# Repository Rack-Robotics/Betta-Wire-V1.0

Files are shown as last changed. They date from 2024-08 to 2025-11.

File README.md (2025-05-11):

# Betta-Wire-V1.0
Betta-Wire V1.0 is an affordable, open-source wire EDM machine designed for enthusiats. It allows users to cut electrically conductive materials such as steel and aluminum without the need for expensive industrial equipment like fiber lasers or CNC machines.

## Features 

- **Open Source**: Fully open-source design, allowing for community contributions and custom modifications.
- **User-3D-Printed**: Most components can be 3D printed, making it accessible and customizable.
- **Powercore Compatible**: Compatible with Powercore V2.0 EDM power supply.
- **4-Axis Motion**: Top and bottom EDM tools are capable of indepedent motion for X, Y, U, & V motion. 
- **Compact Build Area**: 100mm x 200mm, suitable for moderate-scale projects.
- **Hole Popping**: Cut starter holes for enclosed profiles using 1mm diameter hole popping electrodes.
- **Assisted Threading**: Easy controls for beginning threading and for detecting successful threading.
- **Material Compatibility**: Capable of cutting aluminum, steel, titanium, and other electrically conductive materials.

## Revisions 

### RevA

RevA is the prototype proof-of-concept version of the Betta-Wire V1.0. It served as the initial platform to test and validate the core functionality of the machine. While functional, it lacks some of the refinements and optimizations planned for the final kit version.

### RevB

RevB is the branch for the final version that will be used for the kit. This version includes all the improvements and optimizations based on the learnings from RevA. It is intended for distribution to users who will assemble the Betta-Wire V1.0 from the kit.

## Recommended Prerequisites

- 3D Printer (capable of printing carbon fiber PLA)
- Basic understanding of mechatronics and 3D printing
- Familiarity with Klipper firmware
 
 ## Legal & License

Shield: [][cc-by-nc]

This work is licensed under a
[Creative Commons Attribution-NonCommercial 4.0 International License][cc-by-nc].

[][cc-by-nc]

[cc-by-nc]: https://creativecommons.org/licenses/by-nc/4.0/
[cc-by-nc-image]: https://licensebuttons.net/l/by-nc/4.0/88x31.png
[cc-by-nc-shield]: https://img.shields.io/badge/License-CC%20BY--NC%204.0-lightgrey.svg

You are free to:
- Share — copy and redistribute the material in any medium or format
- Adapt — remix, transform, and build upon the material

Under the following terms:
- Attribution — You must give appropriate credit, provide a link to the license, and indicate if changes were made. You may do so in any reasonable manner, but not in any way that suggests the licensor endorses you or your use.
- NonCommercial — You may not use the material for commercial purposes.

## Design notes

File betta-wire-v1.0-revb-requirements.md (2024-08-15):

# Betta Wire V1.0, RevB Requirements
This document is for the recording of requirements for the Betta Wire V1.0, RevB. Requirements are organized by category, assembly, or component. All requirements must have a description and owner. Requirement headings are optimized for hyperlink referencing in other documents.  

## System Requirements
System-level requirements for the Betta Wire V1.0 RevB. This includes general constraints, such as system voltage or firmware.

| Requirement | Description | Owner | Importance | Rational |
| :---| :---| :---| :---| :---|
| Klipper Firmware | Use Klipper firmware | John (Rack Robotics)  | Mandatory | [Design Decision](Design-Decisions.md##Firmware)  |
| System Voltage | 24 VDC | John (Rack Robotics)  | Preferred | Industry Standard for FDM 3D printers | 
| EDM Wire Diameter | 0.3 mm | John (Rack Robotics)  | Preferred | [Design Decision](Design-Decisions.md##EDM-Wire)  | 

## Hardware Requirements
Requirements for hardware, such as fasteners. 
| Requirement | Description | Owner | Importance | Rational |
| :---| :---| :---| :---| :---|
| Fastener Material | Stainless Steel 316L (2) > Stainless Steel 304 | John (Rack Robotics)  | Mandatory | Resistance against corrosion in distilled water | 
| Fasteners Count | Minimize quantity & diversity of fasteners | John (Rack Robotics)  | Mandatory | Minimize cost and complexity | 
| Fastener Style | Metric, DIN 7991 Countersunk | John (Rack Robotics)  | Preferred | Flush mounting of fasteners in FDM prints |
| Fastener Type(s) | Pins > Countersunk M3 > Countersunk M4 > Countersunk M5 > Countersunk M6 | John (Rack Robotics)  | Mandatory | Minimize cost and complexity |

## 3D Printer Requirements
Requirements for 3D printing Betta Wire V1.0 components. The Betta Wire V1.0 is sold as a hardware kit, in the style of Voron. The plastic components are printed by the customer. This reduces kit cost significantly, and allows for user to customize their build's color scheme or materials.

> WARNING: CF-PA (carbon-fiber nylon) is not suitable for use on the Betta Wire or Wire Tool. CF-PA Filament deteriorates rapidly in water, loosing mechanical stiffness within days. Parts printed in CF-PA cannot be submerged in water. 

| Requirement | Description | Owner | Importance | Rational |
| :---| :---| :---| :---| :---|
| Minimum 3D Printer Build Area | X210 mm x Y210 mm x Z200 mm | John (Rack Robotics)  | Mandatory | Compatibility with common 3D printer build volumes|
| Recommended 3D Printer | Prusa MK4/MK3, Bambu X1C, Bambu P1P | John (Rack Robotics)  | Mandatory | Compatibility with common 3D printer build volumes|
| Recommended Filament | [CF-PLA](https://us.store.bambulab.com/products/pla-cf?variant=41003202248840) | John (Rack Robotics)  | Preferred | Excellent quality, minimum warping | 
| Alternative Filament | [ASA](https://www.prusa3d.com/category/prusament-asa/) | John (Rack Robotics)  | Preferred | Minimal warping compared to ABS |

## Hand Tool Requirements 
Requirements for hand tools for user assembly. 
| Requirement | Description | Owner |
| :---| :---| :---|
| Metric Allen Key Set | Allen key set for assembly of metric fasteners | John (Rack Robotics)  |
| Metric Drill Bits for Plastic | M5, M4, & M3 Drill bits for sizing holes in FDM 3D prints | John (Rack Robotics)  |
| Hand drill | Small handheld drill for drill bits | John (Rack Robotics)  |
| Gloves | Disposable gloves for applying super-glue and corrosion inhibitor | John (Rack Robotics)  |

## Controls Requirements 
Control requirements for the Betta Wire V1.0 RevB. Methods used to manage and direct the behavior of the machine and devices to achieve desired outputs. 

| Requirement | Description | Owner | Importance | Rational |
| :---| :---| :---| :---| :---|
| Open-Loop Motion Planning | Open-loop control of linear motion axis | John (Rack Robotics)  | Mandatory | [Design Decision](Design-Decisions.md###Why-not-closed-loop-motors-for-kinematics?) | 
| Open-Loop Wire Velocity | Open-loop control of EDM wire velocity | John (Rack Robotics)  | Preferred | Outside of project scope | 
| Closed-Loop Wire Tension | Maintain wire tension using closed-loop control | John (Rack Robotics)  | Mandatory | Improve machining reliability | 
| Closed-Loop Feedrate Control  | Adjust feedrate in response to EDM conditions | John (Rack Robotics)  | Mandatory | Improve machining reliability | 
| EDM PSU E-Shutdown | Automatically shutdown EDM PSU in the event of a prolonged short (PWM > short_threshold) | John (Rack Robotics)  | Mandatory | Safety, protection of PSU | 

## Kinematics
Kinematics requirements for the Betta Wire V1.0 RevB.

| Requirement | Description | Owner | Importance | Rational |
| :---| :---| :---| :---| :---|
| Dual CoreXY | Independently actuated dual coreXY systems | John (Rack Robotics)  | Mandatory | [Design Decision](Design-Decisions.md##RevB-Kinematics | 
| User Maintenance | Ensure means of replacing wear components in gantry | John (Rack Robotics)  | Mandatory | Improve user experience | 
| GT2 Timing Belts | Use GT2 timing belts with glass-core | John (Rack Robotics)  | Mandatory | Industry standard for FDM 3D printers | 
| Timing Belt Material | EPDM Rubber w/ glass-fiber fore | John (Rack Robotics)  | Mandatory | Reduce belt stretching over time | 

## Modules

### Overall Wire EDM Toolhead Requirements
The sender toolhead and receiver toolhead work together to control the position, tension, and velocity of the wire used for EDM cutting.

| Requirement | Description | Owner |
| :---| :---| :---|
| Maximum Tension of Wire | | John (Rack Robotics)  |
| Maximum Velocity of Wire | | John (Rack Robotics)  |
| Minimum Velocity of Wire | | John (Rack Robotics)  |
| Tube for Wire | Use 4 mm OD teflon tubing for wire interconnects | John (Rack Robotics)  |
| [IP68](#P68-Waterproofing) | Use IP68 rated motor for belt drive actuation | John (Rack Robotics)  |
| Testing | Design for testing on stationary test rig | John (Rack Robotics)  |

### Sender Toolhead Module Requirements
Requirements for the sender toolhead of the Betta Wire V1.0 RevB. The top toolhead sits above the water tank, on the bottom gantry. It is responsible for reporting EDM wire tension during machining, feeding new wire through the machine.

| Requirement | Description | Owner |
| :---| :---| :---|
| Belt Drive | Use belts to manipulate EDM wire | John (Rack Robotics)  |
| Tension Sensor | Use load cell for measuring wire tension | John (Rack Robotics)  |
| Energizer | Energize EDM wire with waveforms from Powercore EDM spark generator | John (Rack Robotics)  |
| Tube for Flushing | Use 4 mm OD PU tube for providing delivering 100 PSI water for flushing | John (Rack Robotics)  |

### Receiver Toolhead Module Requirements
Requirements for the receiver toolhead of the Betta Wire V1.0 RevB. The bottom toolhead sits inside the water tank, on the bottom gantry. It is responsible for receiving the EDM wire from the top toolhead, after passing through the cut. 

| Requirement | Description | Owner |
| :---| :---| :---|
| Belt Drive | Use belts to manipulate EDM wire | John (Rack Robotics)  |

### Waterproof Endstop Module
Requirements for waterproof endstops for homing kinematics

| Requirement | Description | Owner |
| :---| :---| :---|
| Hall Effect Sensor | Use a hall-effect sensor for detection of a 6 mm x 2 mm magnet on the toolhead/carriage | John (Rack Robotics)  |

### Wire Spool Box Module

### Waste Wire Box Module

### E-Box Module

## Custom Klipper Modifications

### Closed-Loop Feedrate Control
Requirements for closed-loop feedrate control using Klipper firmware: 

>Closed-loop control is a control-scheme that continuously monitors its output and automatically adjusts its inputs to maintain the desired output, using feedback to correct any deviations from the target performance. This ensures precision and stability in achieving the set goals.

Wire EDM failures often occur because the rate of travel (feedrate) of the electrode outpaces the material-removal rate (MRR). To eliminate this failure mode, the feedrate must be adjusted in response to feedback from the Powercore V2.0 spark generator. The Powercore V2.0 provides feedback using the PWM output port (ALRT). The PWM duty cycle is mapped to the Powercore's "observed spark ignition rate", which is strongly correlated to the material-removal rate. As the material-removal rate increases, the PWM duty cycle increases.

| PWM Duty Cycle | Description | Controls Response | 
| :---| :---| :---|
| 20% | No machining is occurring | Increase feedrate | 
| 80% | Optimum material-removal rate | Maintain feedrate | 
| 100% | Short circuit; EDM wire electrode has crashed into work | Decrease feedrate, or move backwards in program until short is clear  |

To achieve this behavior, new features must be added to Klipper: 

| Requirement | Description | Owner |
| :---| :---| :---|
| Read PWM Duty Cycle | Read PWM duty cycle of GPIO pin on control board, from PC-02 ALRT port | John (Rack Robotics)  |
| Automatic Feedrate Adjustment | Automatically increase/decrease/maintain feedrate in response to PWM duty cycle | John (Rack Robotics)  |
| Display feedback on GUI | Provide machine operator with PWM telemetry | John (Rack Robotics)  |
| Target Feedrate Range | 0.1 mm/min to 64 mm/min | John (Rack Robotics)  |
| Response Time | 100 ms to 1,000 ms | John (Rack Robotics)  |
| Feedrate Acceleration | Rate of change of feedrate must be limited | John (Rack Robotics)  | 
| Powercore V2.0 ALRT Port | 3.3 VDC | John (Rack Robotics)  |
| Powercore V2.0 PWM Frequency  | 10-100 KHz | John (Rack Robotics)  |

### Dual Gantry Motion Section for Klipper
Requirements for new Klipper kinematics module, allowing for independent control of two coreXY gantries. The secondary coreXY system is provides two additional axis: The U-axis and the V-axis. The U-axis is parallel to the X-axis, and the V-axis is parallel to the Y-axis.

| Requirement | Description | Owner |
| :---| :---| :---|
| Dual coreXY Motion Module | Allow for independent control over two coreXY gantries | John (Rack Robotics)  |
| Top coreXY Axis | X-axis & Y-axis | John (Rack Robotics)  | 
| Bottom coreUV Axis | U-axis & V-axis | John (Rack Robotics)  | 
| gcode example | G1 X69 Y420 U69 V420 | John (Rack Robotics)  |

### Wire EDM Toolhead Section for Klipper
Requirements for new Klipper section for use in printer.cfg, to be used for controlling wire tension. 

| Requirement | Description | Owner |
| :---| :---| :---|
| edm_wire_toolhead | Section name | John (Rack Robotics)  | 
| sensor_type | load cell | John (Rack Robotics)  | 
| sensor_range | 5 kg | John (Rack Robotics)  | 
| amplifier | HX711 | John (Rack Robotics)  | 
| control | PID | John (Rack Robotics)  | 
| edm_wire_sender | PWM pin for sender DC motor control | John (Rack Robotics)  | 
| edm_wire_receiver | PWM pin for receiver DC motor control | John (Rack Robotics)  | 
| mainsail telemetry | provide load cell value (newtons of force) to user in mainsail GUI (for front end engineer) | John (Rack Robotics)  | 

### Wire EDM Macros

**Macro for "wire_EDM_toolhead_diagnostic"**
Macro to test the maximum tension that the belt drive can provide. At the end of the test, the maximum value, in newtons of force, is printed for the user. 

- inform user 'conducting wire EDM toolhead diagnostic" 
- deactivate sender motor (PWM = 0)
- activate receiver motor (PWM = 255)
- measure load cell reading 
- print load cell value to user in newtons of force

**Macro for "wire_EDM_safe_pause"**
Macro for pausing the program during a wire cutting operation, without moving the tools. 

- inform user "pausing wire EDM"
- print current position of all axis to user
- deactivate EDM PSU to stop high-voltage (disable digital GPIO pin assigned to EDM PSU)
- stop motion 
- lock motors 
- do not home (to avoid crashing wire)

**Macro for "wire_EDM_toolhead_loading"**
Macro for loading wire into the belt drive systems. 

- print message to ask user to load EDM wire into sender
- turn on wire sender DC motor at specified PWM level 
- turn on wire receiver DC motor at specified PWM level 
- wait until the tension detected by the load cell increases, and then begin PID control loop, to make sure the wire is loaded
- stop DC motors 

**Macro for "wire_EDM_toolhead_unloading"**
Macro for unloading wire into the belt drive systems. 

- ask user to cut EDM wire 
- provide section for custom gcode commands
- stop DC motors

## IP68 Waterproofing

>An IP68 rating is an Ingress Protection (IP) code that indicates the degree of protection an electrical enclosure provides against the intrusion of solid objects (like dust) and liquids (like water). The IP code is defined by the International Electrotechnical Commission [(IEC) standard 60529](https://www.iec.ch/ip-ratings).

First Digit (6): Indicates the level of protection against solid particles.
- 6: Dust-tight. No ingress of dust; complete protection against contact (dustproof).

Second Digit (8): Indicates the level of protection against liquids.
- 8: Protection against continuous immersion in water. The equipment is suitable for continuous immersion in water under conditions specified by the manufacturer (usually means it can be submerged beyond 1 meter in depth, often up to 3 meters or more, for a specified period).

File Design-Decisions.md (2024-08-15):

# Betta Wire V1.0 RevB Design Decisions 

This page aims to illustrate the design decisions behind the Betta-Wire V1.0 revision B. This document pertains to RevB, the second revision of Betta Wire V1.0. RevB can be found in the RevB branch of the Betta Wire V1.0 repository. This page gives background information about the key design decisions of RevB only. 

## RevB Overview 
Betta Wire V1.0 RevB is a 4-axis wire EDM machine designed for enthusiasts. It is optimized to provide a low barrier of entry for persons interested in wire EDM for prototyping, and manufacturing robotics.

**Improvements over RevA**
- Improved user experience
- Improved precision
- Improved accuracy
- Reduced setup time 
- Closed-loop wire tension control 
- Closed-loop feedrate control

## RevB Toolheads
The toolheads are subassemblies of the Betta Wire which control the EDM wire. The top toolhead is located on the top gantry. The bottom toolhead is located on the bottom gantry. The toolheads are responsible for controlling wire location, tension, and velocity. 

Design Goals for RevB Wire EDM Toolheads 
- Measure wire tension and report value to control board
- Control wire tension via DC motor
- Control wire velocity via DC motor
- Minimize required volume to improve build space
- Support re-threading of EDM wire without removal of the Betta Wire from the aquarium tank 

The RevB toolheads are inspired by the [Papilio](https://kevinakasam.com/papilio/), a 3D printer extruder optimized for pushing 1.75 mm filament. 

## RevB Kinematics 
The kinematics of the Betta Wire were designed to maximize performance while maintaining a reasonable construction cost.

**Why not linear rails?** Linear rails able to operate underwater are not readily available. To use linear rails, while maintaining a reasonable cost, requires a sub $35 dollar solution.

**Dual Core-XY**: The Betta Wire V1.0 RevB is a dual core-xy machine. Each toolhead is independently controlled by one core-xy system: The four core-xy motors (A, B, C, D) allow for movement in four axis (X, Y, U, V). The top gantry (A & B) moves the top tool, while the bottom gantry (C & D) moves the bottom tool. This permits cutting angles walls, tappers, and chamfers. 

**Remote Power Transmission**: Mechanical power is transmitted from the C & D motors to the bottom gantry by a stainless steel axel. This axel rotates GT2 timing belt pulleys, which actuate the core-xy kinematics remotely. This scheme eliminates the need for water-proof motors, by moving the NEMA 17s above the waterline. Reducing the cost of components here permits resources to be invested into other portions of the Betta Wire, such as the tools and controls.

### Why not closed-loop motors for kinematics? 
Closed-loop motors present a significant control systems challenge for Klipper firmware. Integration of closed-loop motor controls for A, B, C & D motors would require a complete redesign of Klipper’s architecture.

### What is closed-loop feedrate control? 
Closed-loop feedrate control is the adjustment of the rate of machine travel, in response to feedback from the EDM power supply / spark-generator. When the feedrate is too slow, the machine automatically increases speed to optimize the material removal rate. This ensures that the Betta Wire is always cutting at the maximum safe speed.

## General Improvements
General improvements over RevA: 

- Endstops for automatic homing
- Suction-cup mounting of e-box, and other accessory modules for easier assembly and maintenance

## Motherboard & Electronics
- The Manta M5P was chosen for it’s compact integration of a 32-bit microcontroller, up to five motor drivers, and a single-board computer. The dual coreXXY kinematics require 4 motor drivers, leaving 1 motor driver available for future expansions.   

## Firmware 
The Betta Wire V1.0 uses [Klipper](https://www.klipper3d.org) firmware. Klipper permits rapid revisions without the need for recompiling. In addition to a host of features: Wireless connectivity, a GUI, compatibility with most 3D printer control hardware, support for advances sensors, USB, CAN, UART, I2C, and an active development community.

## EDM Power / Spark-Generator 
The Betta Wire V1.0 utilizes the Powercore V1.0 wire EDM power supply. This is an open-source EDM power supply designed and sold by Rack Robotics, Inc.

## EDM Wire
0.3 mm Diameter hardened brass wire was selected as a compromise between maximizing tensile strength, maximizing current capacity, and minimizing cut diameter.

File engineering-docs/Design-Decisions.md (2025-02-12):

# Betta Wire V1.0 RevB Design Decisions 
This page aims to illustrate the design decisions behind the Betta-Wire V1.0 revision B. This page gives background information about the key design decisions of RevB only. 

## RevB Overview 
Betta Wire V1.0 RevB is a 4-axis wire EDM machine designed for enthusiasts. It is optimized to provide a low barrier of entry for persons interested in wire EDM for prototyping, and manufacturing.

**Improvements over RevA**
- Improved user experience
- Improved precision
- Improved accuracy
- Reduced setup time 
- Closed-loop wire tension control 
- Closed-loop feedrate control

## RevB Toolheads
The toolheads are subassemblies of the Betta Wire which control the EDM wire. The top toolhead is located on the top gantry. The bottom toolhead is located on the bottom gantry. The toolheads are responsible for controlling wire location, tension, and velocity. 

Design Goals for RevB Wire EDM Toolheads 
- Measure wire tension and report value to control board
- Control wire tension via DC motor
- Control wire velocity via DC motor
- Minimize required volume to improve build space
- Support semi-automiatic re-threading of EDM wire

The RevB toolheads are inspired by the [Papilio](https://kevinakasam.com/papilio/), a 3D printer extruder optimized for pushing 1.75 mm filament. 

## RevB Kinematics
The kinematics of the Betta Wire were designed to maximize performance while maintaining a reasonable construction cost.

### Why not linear rails?
Linear rails able to operate underwater are not readily available. To use linear rails, while maintaining a reasonable cost, requires a sub $35 dollar solution.

### Dual Core-XY
The Betta Wire V1.0 RevB is a dual core-xy machine. Each toolhead is independently controlled by one core-xy system: The four core-xy motors (A, B, C, D) allow for movement in four axis (X, Y, U, V). The top gantry (A & B) moves the top tool, while the bottom gantry (C & D) moves the bottom tool. This permits cutting angled walls, tappers, and chamfers.

### Remote Power Transmission
Mechanical power is transmitted from the C & D motors to the bottom gantry by a stainless steel axel. This axel rotates GT2 timing belt pulleys, which actuate the core-xy kinematics remotely. This scheme eliminates the need for water-proof motors, by moving the NEMA 17s above the waterline. Reducing the cost of components here permits resources to be invested into other portions of the Betta Wire, such as the tools and controls.

### What is closed-loop feedrate control? 
Closed-loop feedrate control is the adjustment of the rate of machine travel, in response to feedback from the EDM power supply / spark-generator. When the feedrate is too slow, the machine automatically increases speed to optimize the material removal rate. This ensures that the Betta Wire is always cutting at the maximum safe speed.

## General Improvements
General improvements over RevA: 
- Endstops for automatic homing
- Improved kinematics to prevent binding and racking
- Stainless steel components to prevent corrosion

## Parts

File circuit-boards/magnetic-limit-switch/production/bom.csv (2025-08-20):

Designator | Footprint | Quantity | Value | LCSC Part #
C1 | 0603 | 1 | 1 uF | C106248
U1 | SOT-23-3 | 1 | TMAG5231 | C17378950

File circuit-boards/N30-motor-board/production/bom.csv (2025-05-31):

Designator | Footprint | Quantity | Value | LCSC Part #
C1, C2 | 0603 | 2 | 0.1 uF | C113803
J1 | SolderWire-0.25sqmm_1x01_D0.65mm_OD1.7mm | 1 | MOTOR+
J2 | SolderWire-0.25sqmm_1x01_D0.65mm_OD1.7mm | 1 | MOTOR-
M1, M2 | N30_MOTOR_TH | 2 | BDC_N30_MOTOR_01
R1 | 0603 | 1 | 10K | C98220
TP2, TP3, TP4, TP5 | TestPoint_Pad_2.0x2.0mm | 4 | TestPoint

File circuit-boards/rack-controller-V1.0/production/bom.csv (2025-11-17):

Designator | Footprint | Quantity | Value | LCSC Part #
C10, C65, C66, C67, C68, C8, C83, C84 | 0603 | 8 | 0.1uF | C113803
C100, C14, C15, C16, C17, C18, C19, C20, C21, C22, C23, C60, C62, C69, C70, C79, C80, C85, C86, C95, C96, C97, C98, C99 | CP_Elec_6.3x5.9 | 24 | 47u | C264034
C11, C12, C13, C34, C35, C36, C37, C38 | 0603 | 8 | 100nF | C113803
C24, C25, C26, C27, C28, C29, C30, C31, C32, C33, C59, C61, C63, C64, C71, C72, C73, C74, C81, C82, C87, C88, C89, C9, C90, C91, C92, C93, C94 | 1206 | 29 | 10 uF | C96600
C3, C4, C5, C6 | 0603 | 4 | 2.2uF | C106853
C39, C40, C41, C42, C43, C44, C45, C46, C47, C48, C49, C50, C51, C52, C53, C54, C55, C56, C57, C58, C75, C76, C77, C78 | 0402 | 24 | 100pF | C576700
D1, D2, D3, D4, D5 | D_SMC | 5 | SMCJ60A | C2943780
D10, D11, D12, D13, D14, D15, D16, D17, D18, D19, D20, D21, D22, D23, D24, D25, D30, D31, D6, D7, D8, D9 | D_SMA | 22 | SMAJ51CA | C135003
D26, D27, D32 | D_SOD-128 | 3 | PMEG10030ELPX | C5260346
D33 | D_SMA | 1 | US1M-13-F | C99333
HDR1_2, HDR1, HDR2_2, HDR2, HDR3, HDR4, HDR5, HDR6, HDR7, HDR8 | PinSocket_1x08_P2.54mm_Vertical | 10 | PinSocket_1x08_P2.54mm_Vertical | C27438
J1, J17, J18, J19, J9 | 2601-1102 | 5 | 2601-1102
J10, J11, J12, J13, J14, J6 | JST_XH_S4B-XH-SM4-TB_1x04-1MP_P2.50mm_Horizontal_custom | 6 | S4B-XH-SM4-TB | C161861
J15, J16, J2, J3, J4, J5, J7 | S3B-XH-SM4-TB | 7 | S3B-XH-SM4-TB | C161860
J20 | PinHeader_1x03_P2.54mm_Vertical | 1 | BDC_00_SELECTOR | C5360899
J21 | PinHeader_1x03_P2.54mm_Vertical | 1 | BDC_01_SELECTOR | C5360899
J8 | raspberrypi | 1 | Raspberry Pi GPIO Header | NULL
L10, L11, L12, L13, L14, L15, L16, L17, L18, L19, L20, L21, L22, L23, L24, L27, L28, L29, L30, L31, L5, L6, L7, L8, L9 | 0402 | 25 | BBUP00100505330Y00 | C668299
L25, L26, L32 | SRR1210-8R2Y | 3 | 8.2 uH
R1, R100, R104, R18, R19, R2, R22, R23, R26, R27, R30, R31, R34, R35, R5, R6, R7, R8, R9, R96, R98 | 0603 | 21 | 1K | C22548
R10, R11, R12, R13, R14, R16, R20, R24, R28, R3, R32, R36, R37, R38, R39, R4, R40, R41, R43, R45, R47, R49, R51, R52, R53, R54, R55, R56, R92, R93, R94 | 0603 | 31 | 10K | C98220
R101, R102, R103 | 0603 | 3 | 19.6K | C245925
R57, R58, R59, R60, R61, R62, R63, R64, R65, R66, R67, R68, R69, R70, R71, R72, R73, R74, R75, R76, R85, R86, R87, R88 | 0603 | 24 | 150R | C114608
R77, R78, R89 | 0603 | 3 | 49.9K
R79, R81, R90 | 0603 | 3 | 100K | C728638
R80, R82 | 0603 | 2 | 9.09K | C185301
R83, R84 | 2512 | 2 | 0.11R | C46595965
R91 | 0603 | 1 | 17.8K | C185364
R95, R97, R99 | 0603 | 3 | 2.2K | C114662
RP4 | raspberrypi-outline | 1 | Raspberry_Pi
U1, U2, U3, U4, U5 | BTT_TMC2209_V1.3 | 5 | TMC2209_SILENTSTEPSTICK | NULL
U10, U6, U7 | LV14360PDDAR | 3 | LV14360PDDAR | C2864599
U11, U12, U13 | TPS1HTC30-Q1 | 3 | TPS1HTC30AQPWPRQ1 | C22414694
U8, U9 | DRV8870DDA | 2 | DRV8870DDA | C86590

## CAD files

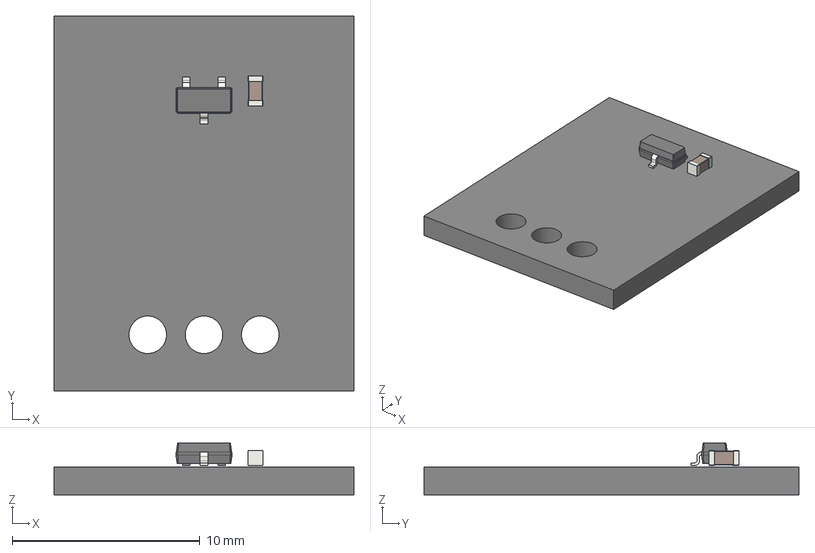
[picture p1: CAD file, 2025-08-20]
circuit-boards/magnetic-limit-switch/3D-models/magnetic-limit-switch-D.step
16.0 x 20.0 x 2.76 mm
SOT-23-3
C_0603_1608Metric
magnetic-limit-switch_PCB

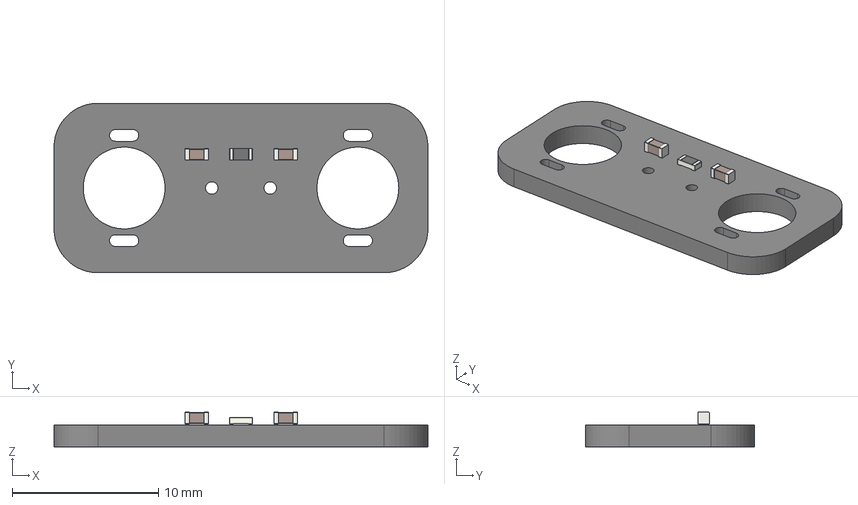
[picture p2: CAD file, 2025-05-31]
circuit-boards/N30-motor-board/production/N30-motor-board-RevA.step
25.6 x 11.6 x 2.37 mm
C_0603_1608Metric x 2
R_0603_1608Metric
N30-motor-board_PCB

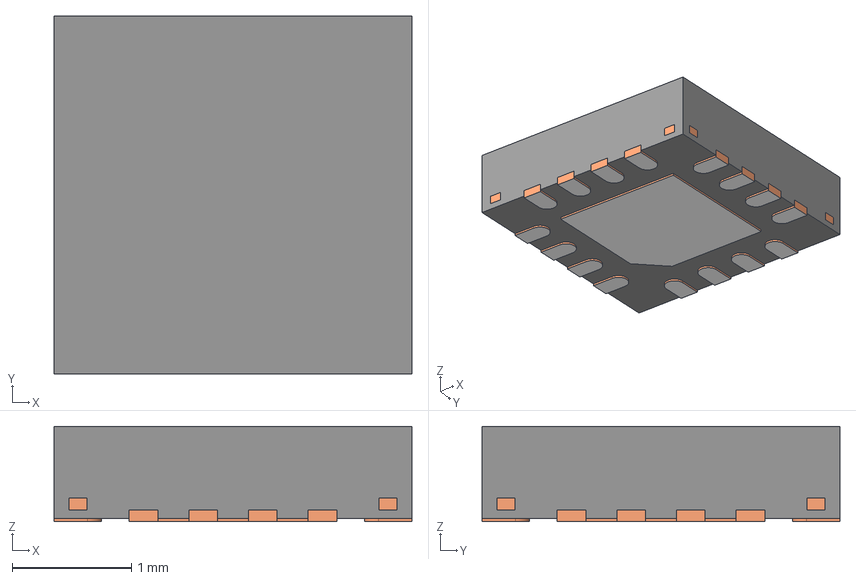
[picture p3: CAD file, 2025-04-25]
circuit-boards/rack-controller-V1.0/3D-models/DRV8235RTER.stp
3.00 x 3.00 x 0.8 mm
BODY-QFN
FRAME-RTE0016C
PIN1-ID

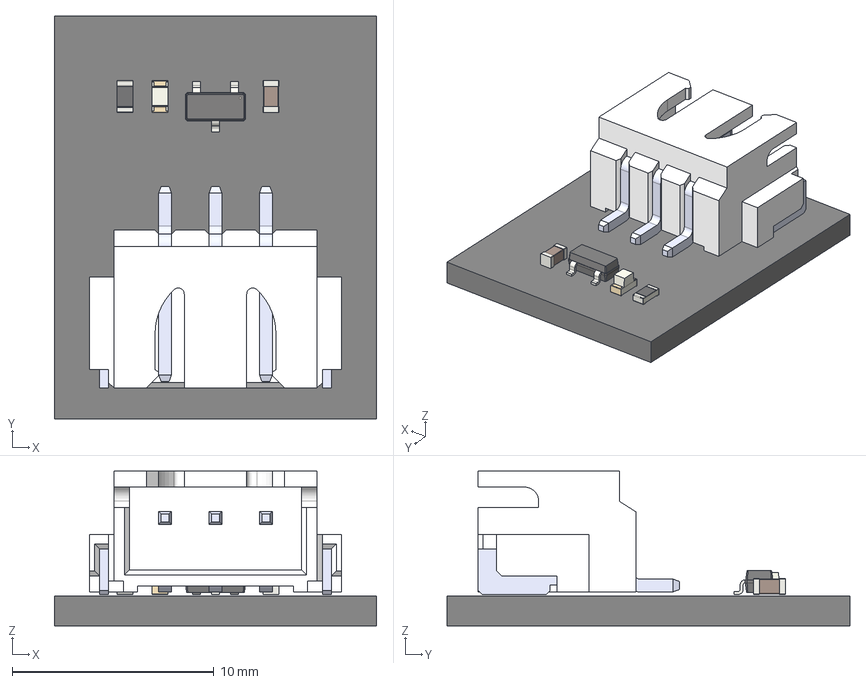
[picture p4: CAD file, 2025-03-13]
circuit-boards/magnetic-limit-switch/3D-models/magnetic-limit-switch-C.step
16.0 x 20.0 x 7.69 mm
SOT-23-3
SxB-XH-SM4-TB_3
pin^SxB-XH-SM4-TB Ass x 3
R_0603_1608Metric
C_0603_1608Metric
LED_0603_1608Metric
magnetic-limit-switch_PCB

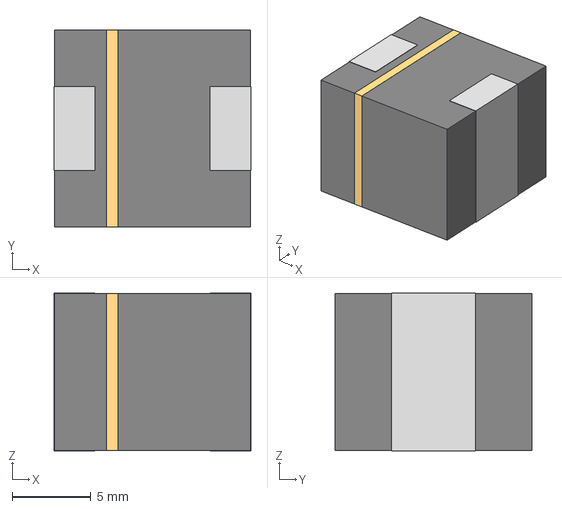
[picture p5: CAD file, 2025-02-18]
circuit-boards/rack-controller-V1.0/3D-models/SRR1210-8R2Y.step
12.5 x 12.5 x 10.0 mm

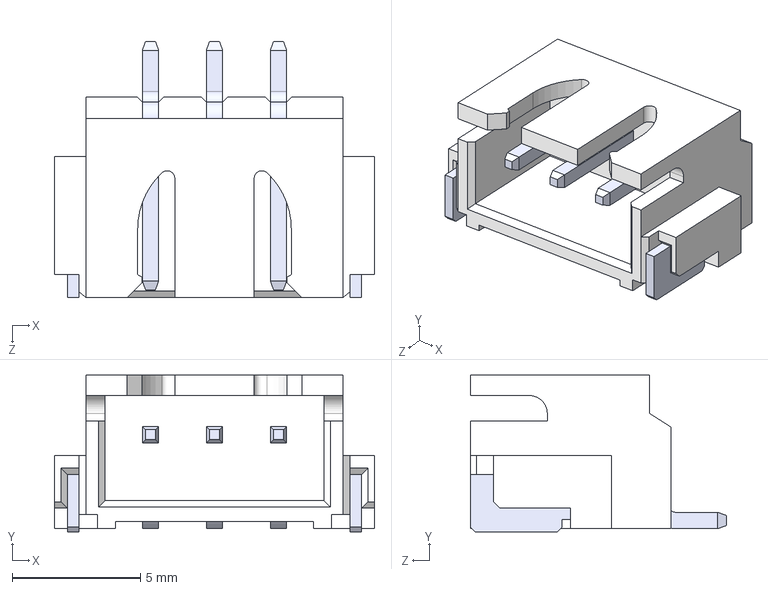
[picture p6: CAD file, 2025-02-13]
circuit-boards/magnetic-limit-switch/3D-models/S3B-XH-SM4-TB.STEP
12.5 x 6.12 x 10.0 mm
SxB-XH-SM4-TB_3
pin^SxB-XH-SM4-TB Ass x 3

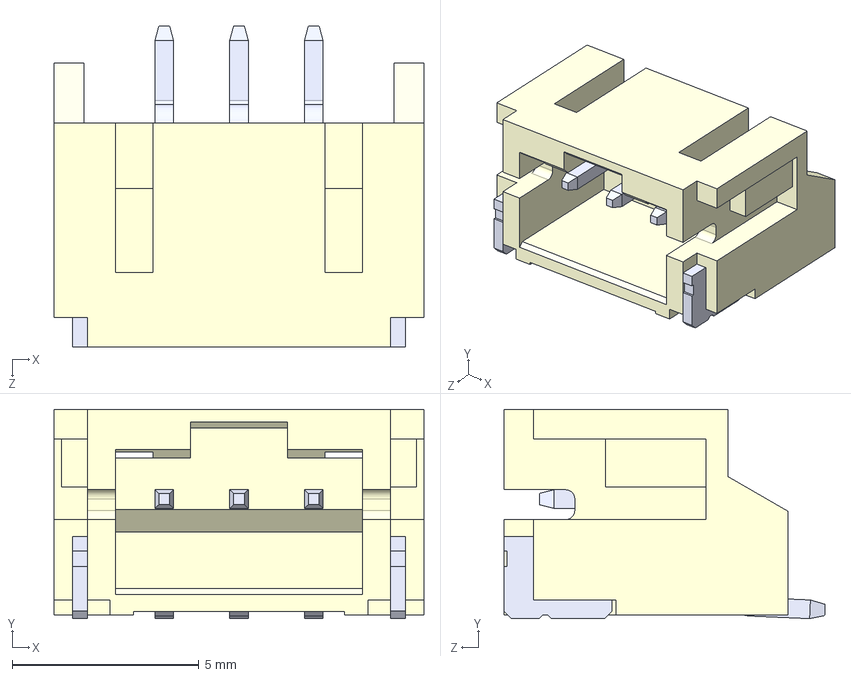
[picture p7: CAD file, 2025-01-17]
circuit-boards/magnetic-limit-switch/3D-models/S3B-PH-SM4-TB.step
9.90 x 5.60 x 8.60 mm

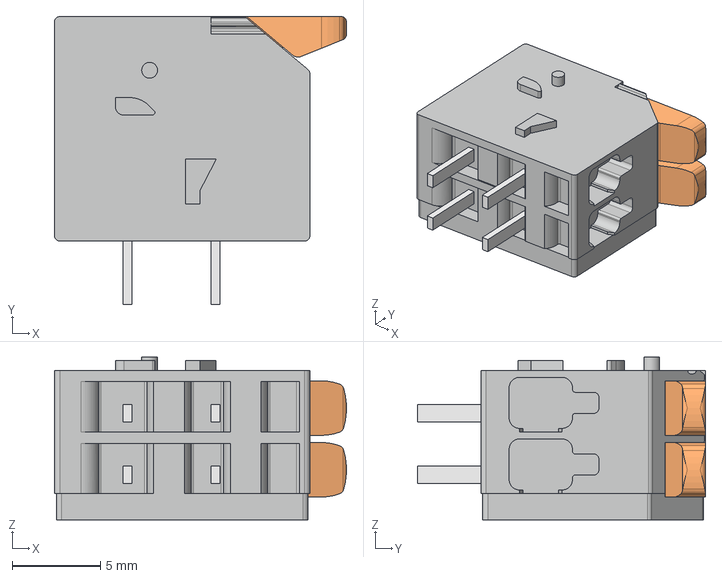
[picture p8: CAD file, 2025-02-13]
circuit-boards/rack-controller-V1.0/3D-models/2601-1102.stp
16.6 x 16.4 x 9.25 mm

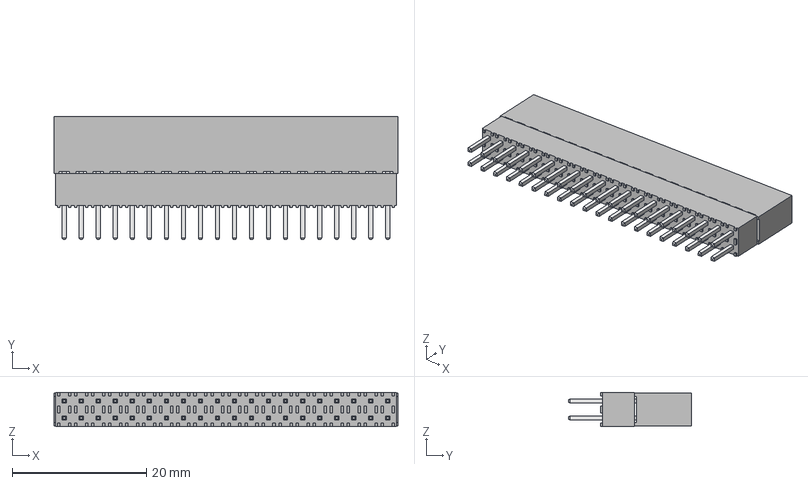
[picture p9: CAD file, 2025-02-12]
circuit-boards/rack-controller-V1.0/3D-models/ESQ-120-23-T-D.step
51.3 x 18.4 x 5.08 mm
ESQ-120-23-T-D_socket
ESQ-120-23-T-D_pins
ESQ-120-23-T-D2_pins
ESQ-120-23-G-D-LL_bpins

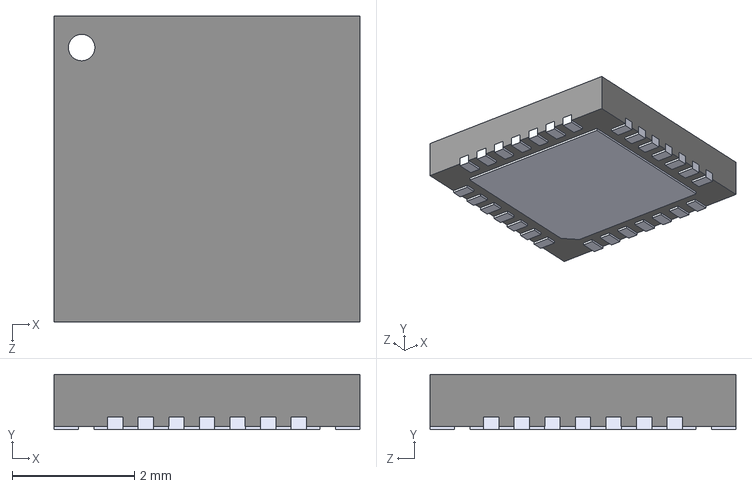
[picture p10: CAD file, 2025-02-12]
circuit-boards/rack-controller-V1.0/3D-models/TMC2209-LA.step
5.00 x 0.9 x 5.00 mm

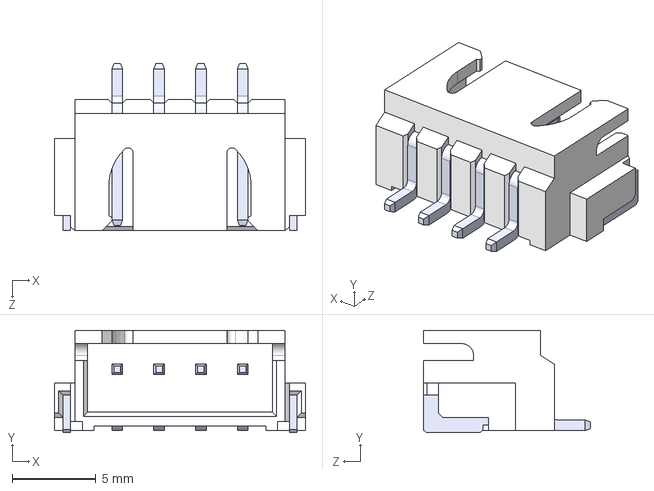
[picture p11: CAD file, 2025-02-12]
circuit-boards/rack-controller-V1.0/3D-models/S4B-XH-SM4-TB.STEP
15.0 x 6.12 x 10.0 mm
SxB-XH-SM4-TB_4
pin^SxB-XH-SM4-TB Ass x 4

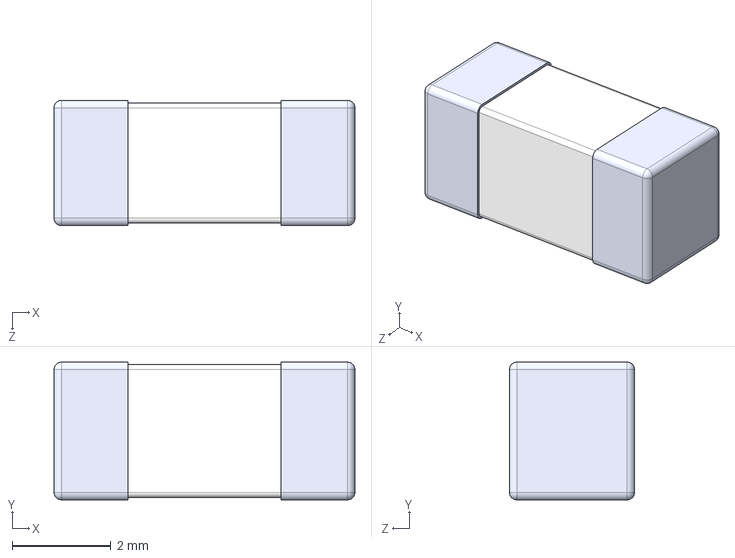
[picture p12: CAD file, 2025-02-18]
circuit-boards/rack-controller-V1.0/3D-models/0679H9120-05.step
6.10 x 2.79 x 2.54 mm

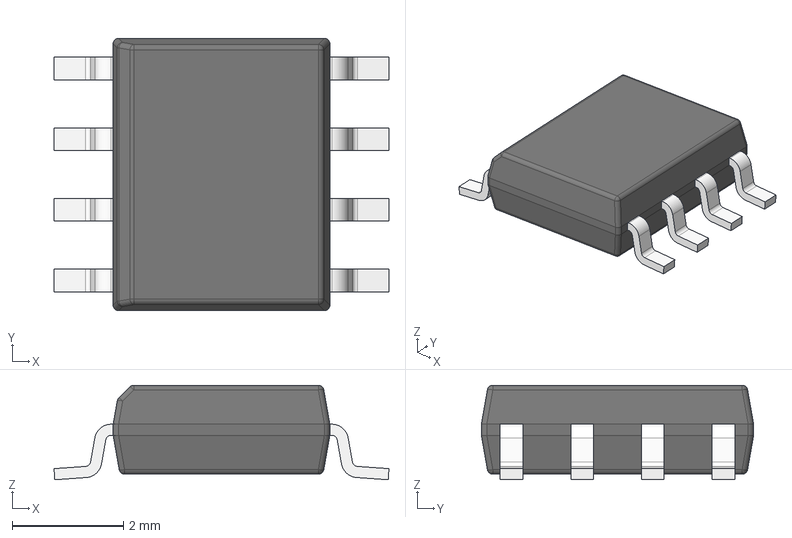
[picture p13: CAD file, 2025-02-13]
circuit-boards/rack-controller-V1.0/3D-models/LMR36520ADDAR.stp
6.03 x 4.90 x 1.70 mm
BODY-SO
LEAD-SO x 8
THERMALPAD-SO

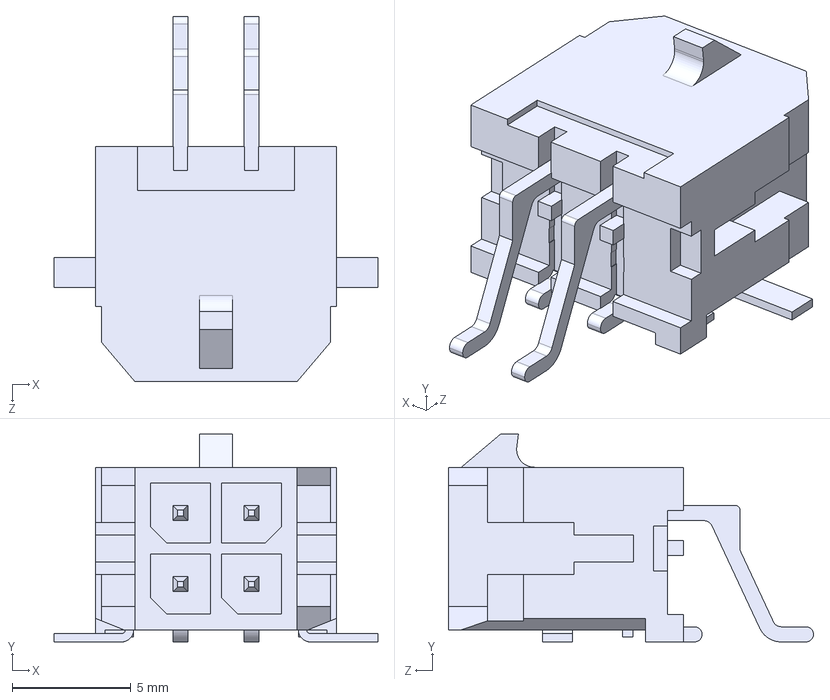
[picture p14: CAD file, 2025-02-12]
circuit-boards/rack-controller-V1.0/3D-models/430450409.step
13.7 x 8.77 x 15.4 mm
043045xxxx_04
tab^043045xxxx ass
pin^043045xxxx ass x 2

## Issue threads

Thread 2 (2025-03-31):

add to features

mkinney, 2025-03-31:
Reading back on the discord, it looks like these features are going to be present:
- assisted threading
- hole popping

Might want to add that to the features

Cooper-RackRobo, 2025-05-05:
Good idea. Added.

Closed 2025-05-05.

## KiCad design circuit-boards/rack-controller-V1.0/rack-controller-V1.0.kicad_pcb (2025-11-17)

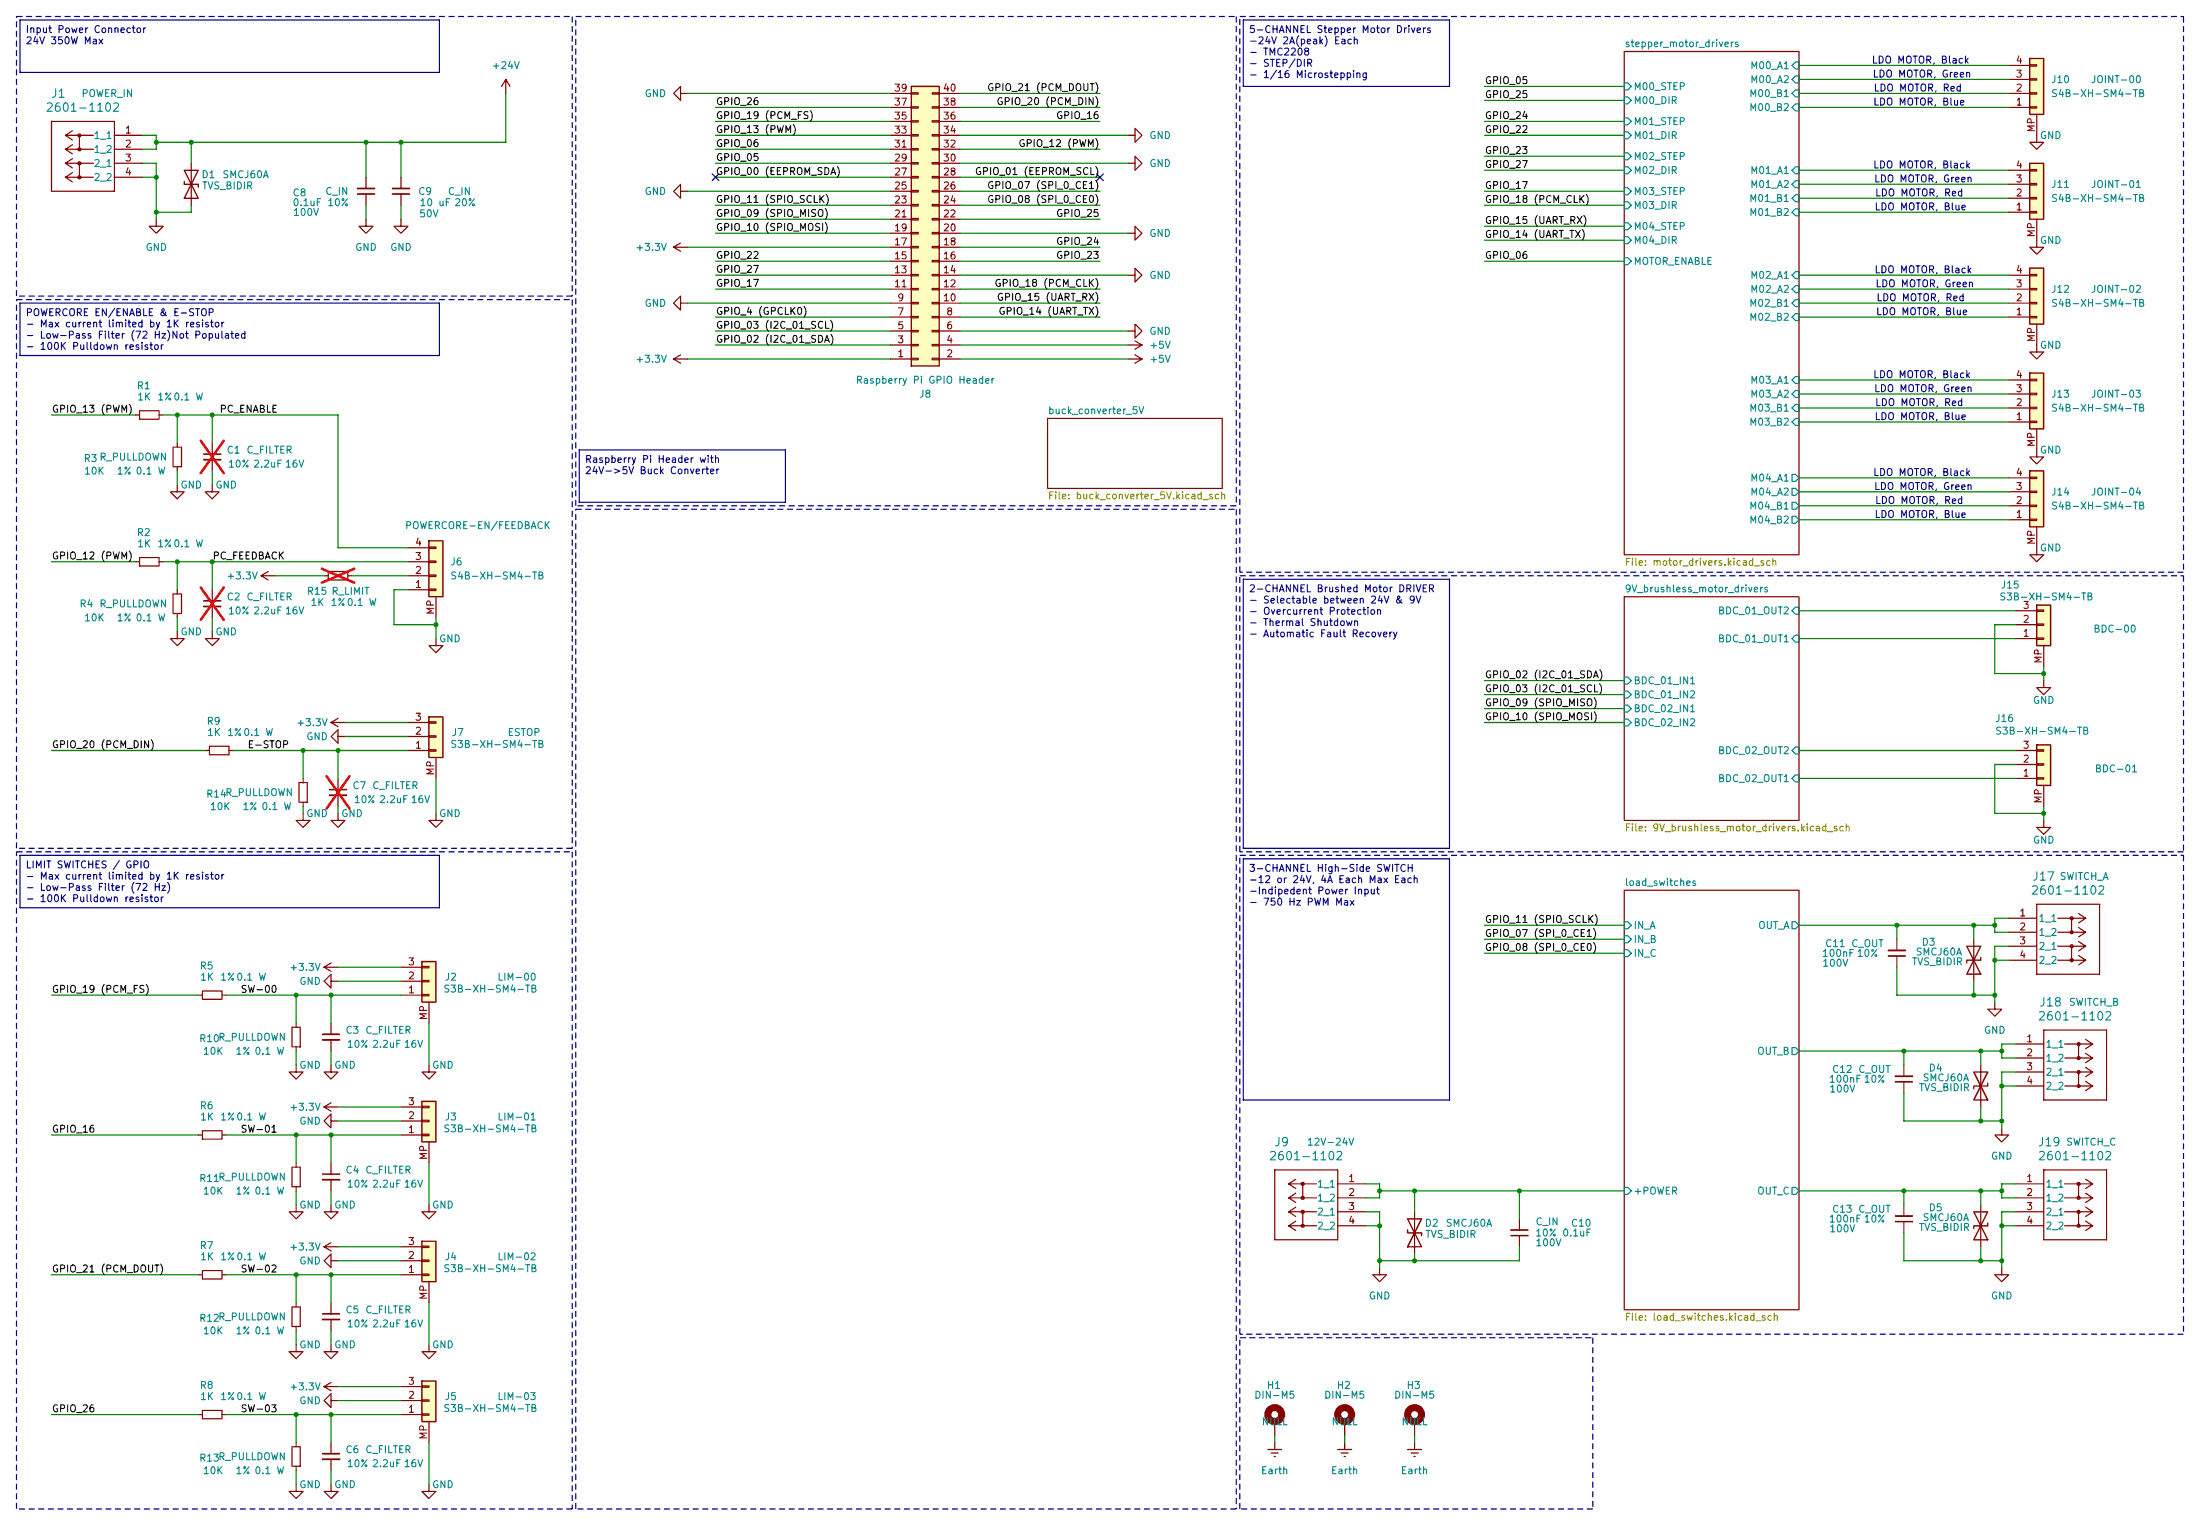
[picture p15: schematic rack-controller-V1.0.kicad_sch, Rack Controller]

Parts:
C1, C2, C7: 2.2uF; C_0603_1608Metric; Max Voltage 16V; Tolerance 10%; Manufacturer# CC0603KRX5R7BB225; LCSC Part # C106853; not fitted
C3, C4, C5, C6: 2.2uF; C_0603_1608Metric; Max Voltage 16V; Tolerance 10%; Manufacturer# CC0603KRX5R7BB225; LCSC Part # C106853
C8, C10: 0.1uF; C_0603_1608Metric; Tolerance 10%; Max Voltage 100V; Manufacturer# CC0603KRX7R0BB104; LCSC Part # C113803
C9: 10 uF; C_1206_3216Metric; Tolerance 20%; Max Voltage 50V; Manufacturer# CL31A106MBHNNNE; LCSC Part # C96600
C11, C12, C13: 100nF; C_0603_1608Metric; Voltage 100V; Tolerance 10%; Manufacturer# CC0603KRX7R0BB104; LCSC Part # C113803
D1, D2, D3, D4, D5: SMCJ60A; D_SMC; Manufacturer# SMCJ60CA-13-F; LCSC Part # C2943780
H1, H2, H3: DIN-M5; MountingHole_5.3mm_M5_DIN965_Pad_TopBottom; Manufacturer# NULL; LCSC Part # NULL
J1, J9, J17, J18, J19: 2601-1102; Manufacturer# 2601-1102
J2, J3, J4, J5, J7, J15, J16: S3B-XH-SM4-TB; Manufacturer# JST Sales America Inc.; LCSC Part # C161860
J6, J10, J11, J12, J13, J14: S4B-XH-SM4-TB; JST_XH_S4B-XH-SM4-TB_1x04-1MP_P2.50mm_Horizontal_custom; Manufacturer# S4B-XH-SM4-TB; LCSC Part # C161861
J8: Raspberry Pi GPIO Header; raspberrypi; Manufacturer# ESQ-120-23-T-D; LCSC Part # NULL
R1, R2, R5, R6, R7, R8, R9: 1K; R_0603_1608Metric; Tolerance 1%; Manufacturer# RC0603FR-071KL; LCSC Part # C22548
R3, R4, R10, R11, R12, R13, R14: 10K; R_0603_1608Metric; Tolerance 1%; Manufacturer# RC0603BR-0710KL; LCSC Part # C98220
R15: 1K; R_0603_1608Metric; Tolerance 1%; Manufacturer# RC0603FR-071KL; LCSC Part # C22548; not fitted

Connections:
+3.3V: J2.3, J3.3, J4.3, J5.3, J7.3, J8.1, J8.17, R15.1; also elsewhere on the board
+5V: J8.2, J8.4; also elsewhere on the board
+24V: C8.2, C9.2, D1.2 (A2), J1.1 (1_1), J1.2 (1_2); also elsewhere on the board
/9V_brushless_motor_drivers/BDC_01_OUT1: J15.1; also elsewhere on the board
/9V_brushless_motor_drivers/BDC_01_OUT2: J15.3; also elsewhere on the board
/9V_brushless_motor_drivers/BDC_02_OUT1: J16.1; also elsewhere on the board
/9V_brushless_motor_drivers/BDC_02_OUT2: J16.3; also elsewhere on the board
/E-STOP: C7.1, J7.1, R9.2, R14.2
/GPIO_00 (EEPROM_SDA): J8.27
/GPIO_01 (EEPROM_SCL): J8.28
/GPIO_02 (I2C_01_SDA): J8.3; also elsewhere on the board
/GPIO_03 (I2C_01_SCL): J8.5; also elsewhere on the board
/GPIO_4 (GPCLK0): J8.7
/GPIO_05: J8.29; also elsewhere on the board
/GPIO_06: J8.31; also elsewhere on the board
/GPIO_07 (SPI_0_CE1): J8.26; also elsewhere on the board
/GPIO_08 (SPI_0_CE0): J8.24; also elsewhere on the board
/GPIO_09 (SPIO_MISO): J8.21; also elsewhere on the board
/GPIO_10 (SPIO_MOSI): J8.19; also elsewhere on the board
/GPIO_11 (SPIO_SCLK): J8.23; also elsewhere on the board
/GPIO_12 (PWM): J8.32, R2.1
/GPIO_13 (PWM): J8.33, R1.1
/GPIO_14 (UART_TX): J8.8; also elsewhere on the board
/GPIO_15 (UART_RX): J8.10; also elsewhere on the board
/GPIO_16: J8.36, R6.1
/GPIO_17: J8.11; also elsewhere on the board
/GPIO_18 (PCM_CLK): J8.12; also elsewhere on the board
/GPIO_19 (PCM_FS): J8.35, R5.1
/GPIO_20 (PCM_DIN): J8.38, R9.1
/GPIO_21 (PCM_DOUT): J8.40, R7.1
/GPIO_22: J8.15; also elsewhere on the board
/GPIO_23: J8.16; also elsewhere on the board
/GPIO_24: J8.18; also elsewhere on the board
/GPIO_25: J8.22; also elsewhere on the board
/GPIO_26: J8.37, R8.1
/GPIO_27: J8.13; also elsewhere on the board
/PC_ENABLE: C1.1, J6.4, R1.2, R3.2
/PC_FEEDBACK: C2.1, J6.3, R2.2, R4.2
/SW-00: C3.1, J2.1, R5.2, R10.2
/SW-01: C4.1, J3.1, R6.2, R11.2
/SW-02: C5.1, J4.1, R7.2, R12.2
/SW-03: C6.1, J5.1, R8.2, R13.2
/load_switches/+POWER: C10.2, D2.2 (A2), J9.1 (1_1), J9.2 (1_2); also elsewhere on the board
/load_switches/OUT_A: C11.2, D3.2 (A2), J17.1 (1_1), J17.2 (1_2); also elsewhere on the board
/load_switches/OUT_B: C12.2, D4.2 (A2), J18.1 (1_1), J18.2 (1_2); also elsewhere on the board
/load_switches/OUT_C: C13.2, D5.2 (A2), J19.1 (1_1), J19.2 (1_2); also elsewhere on the board
/stepper_motor_drivers/M00_A1: J10.4; also elsewhere on the board
/stepper_motor_drivers/M00_A2: J10.3; also elsewhere on the board
/stepper_motor_drivers/M00_B1: J10.2; also elsewhere on the board
/stepper_motor_drivers/M00_B2: J10.1; also elsewhere on the board
/stepper_motor_drivers/M01_A1: J11.4; also elsewhere on the board
/stepper_motor_drivers/M01_A2: J11.3; also elsewhere on the board
/stepper_motor_drivers/M01_B1: J11.2; also elsewhere on the board
/stepper_motor_drivers/M01_B2: J11.1; also elsewhere on the board
/stepper_motor_drivers/M02_A1: J12.4; also elsewhere on the board
/stepper_motor_drivers/M02_A2: J12.3; also elsewhere on the board
/stepper_motor_drivers/M02_B1: J12.2; also elsewhere on the board
/stepper_motor_drivers/M02_B2: J12.1; also elsewhere on the board
/stepper_motor_drivers/M03_A1: J13.4; also elsewhere on the board
/stepper_motor_drivers/M03_A2: J13.3; also elsewhere on the board
/stepper_motor_drivers/M03_B1: J13.2; also elsewhere on the board
/stepper_motor_drivers/M03_B2: J13.1; also elsewhere on the board
/stepper_motor_drivers/M04_A1: J14.4; also elsewhere on the board
/stepper_motor_drivers/M04_A2: J14.3; also elsewhere on the board
/stepper_motor_drivers/M04_B1: J14.2; also elsewhere on the board
/stepper_motor_drivers/M04_B2: J14.1; also elsewhere on the board
Earth: H1.1, H2.1, H3.1
GND: C1.2, C2.2, C3.2, C4.2, C5.2, C6.2, C7.2, C8.1, C9.1, C10.1, C11.1, C12.1, C13.1, D1.1 (A1), D2.1 (A1), D3.1 (A1), D4.1 (A1), D5.1 (A1), J1.3 (2_1), J1.4 (2_2), J2.2, J2.MP, J3.2, J3.MP, J4.2, J4.MP, J5.2, J5.MP, J6.1, J6.MP, J7.2, J7.MP, J8.6, J8.9, J8.14, J8.20, J8.25, J8.30, J8.34, J8.39, J9.3 (2_1), J9.4 (2_2), J10.MP, J11.MP, J12.MP, J13.MP, J14.MP, J15.2, J15.MP, J16.2, J16.MP, J17.3 (2_1), J17.4 (2_2), J18.3 (2_1), J18.4 (2_2), J19.3 (2_1), J19.4 (2_2), R3.1, R4.1, R10.1, R11.1, R12.1, R13.1, R14.1; also elsewhere on the board
unnamed: J6.2, R15.2

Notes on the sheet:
LDO MOTOR, Green
LDO MOTOR, Blue
LDO MOTOR, Black
LDO MOTOR, Red
2-CHANNEL Brushed Motor DRIVER - Selectable between 24V & 9V - Overcurrent Protection - Thermal Shutdown - Automatic Fault Recovery
LIMIT SWITCHES / GPIO - Max current limited by 1K resistor - Low-Pass Filter (72 Hz) - 100K Pulldown resistor
5-CHANNEL Stepper Motor Drivers -24V 2A(peak) Each - TMC2208 - STEP/DIR - 1/16 Microstepping
POWERCORE EN/ENABLE & E-STOP - Max current limited by 1K resistor - Low-Pass Filter (72 Hz)Not Populated - 100K Pulldown resistor
3-CHANNEL High-Side SWITCH -12 or 24V, 4A Each Max Each -Indipedent Power Input - 750 Hz PWM Max
Input Power Connector 24V 350W Max
Raspberry Pi Header with 24V->5V Buck Converter

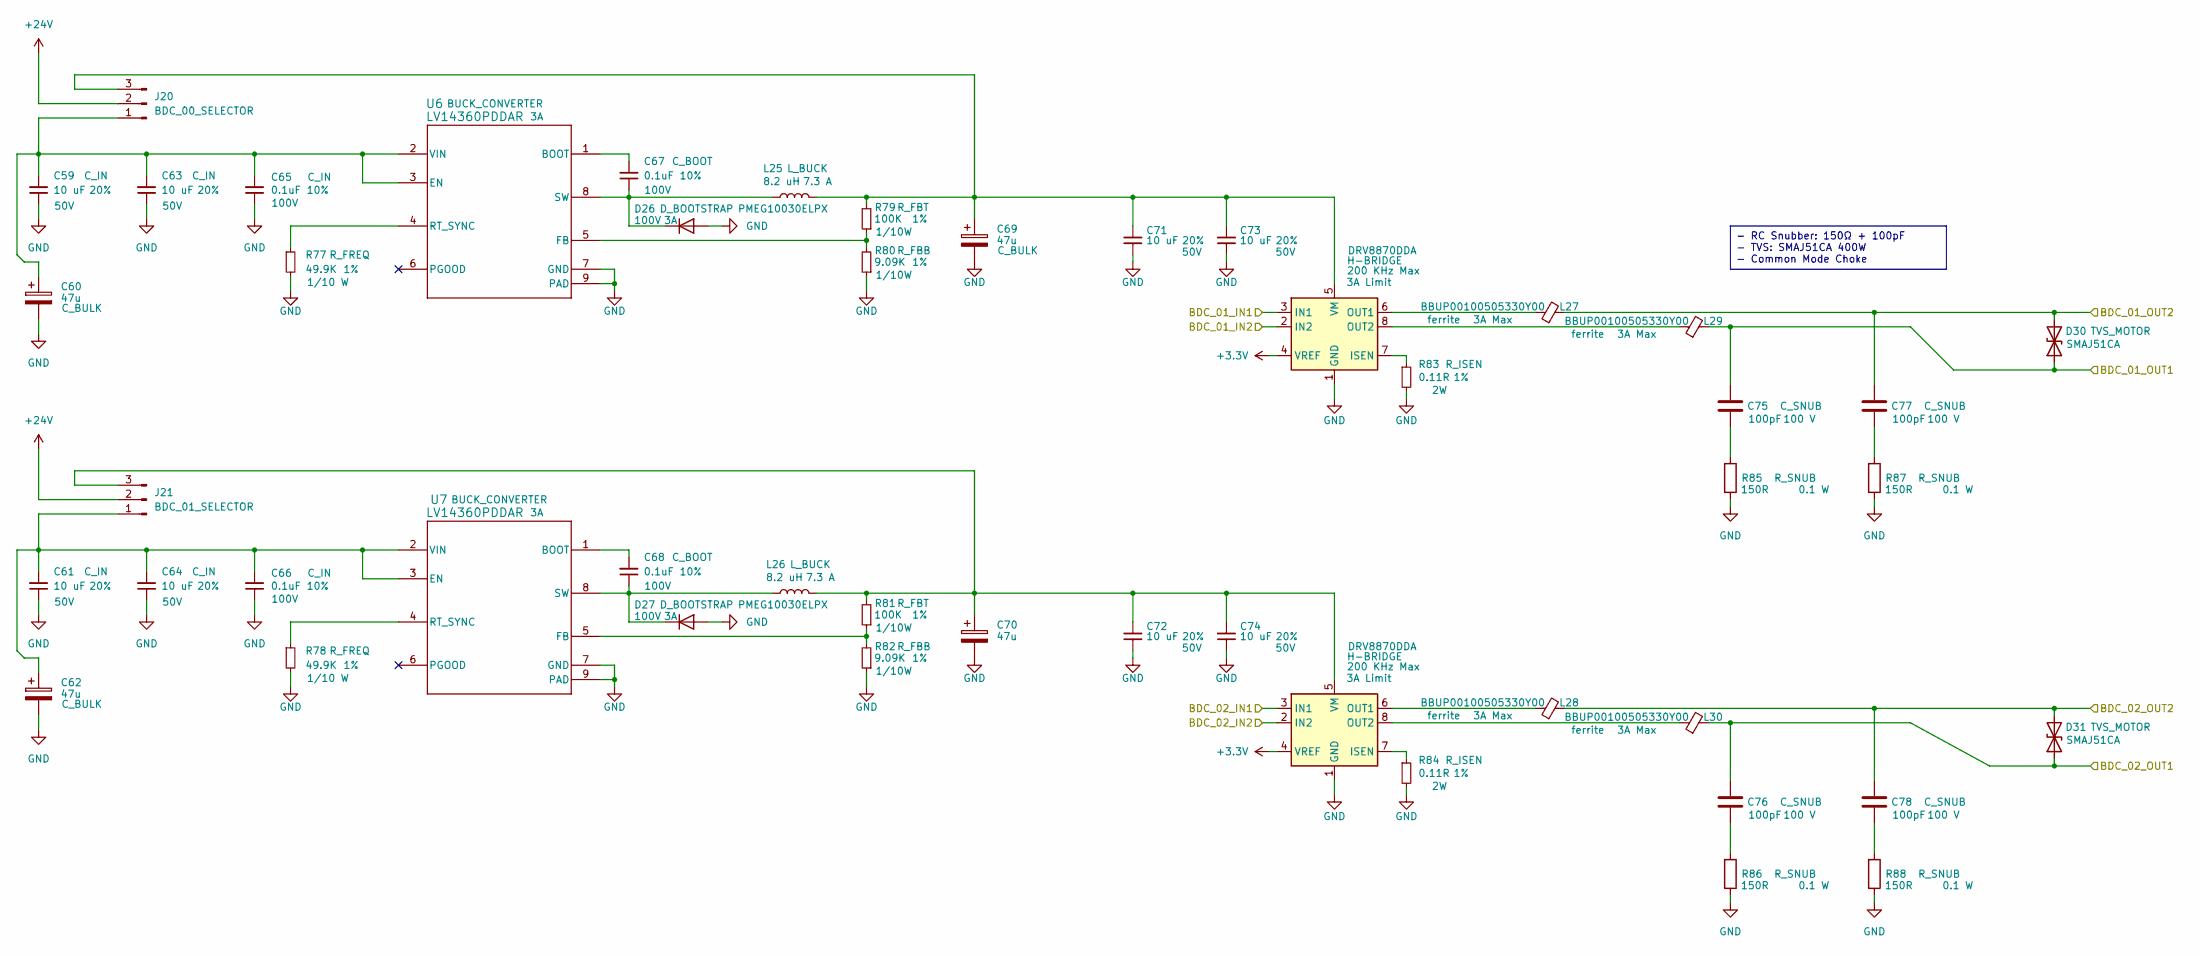
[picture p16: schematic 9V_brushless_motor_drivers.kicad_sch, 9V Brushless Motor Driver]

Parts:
C59, C61, C63, C64, C71, C72, C73, C74: 10 uF; C_1206_3216Metric; Tolerance 20%; Max Voltage 50V; Manufacturer# CL31A106MBHNNNE; LCSC Part # C96600
C60, C62, C69, C70: 47u; CP_Elec_6.3x5.9; Manufacturer# 35SVPK47M; LCSC Part # C264034
C65, C66, C67, C68: 0.1uF; C_0603_1608Metric; Tolerance 10%; Max Voltage 100V; Manufacturer# CC0603KRX7R0BB104; LCSC Part # C113803
C75, C76, C77, C78: 100pF; C_0402_1005Metric; Voltage 100 V; Manufacturer# CC0402JRNPO0BN101; LCSC Part # C576700
D26, D27: PMEG10030ELPX; D_SOD-128; Max Voltage 100V; Manufacturer# PMEG10030ELPX; LCSC Part # C5260346
D30, D31: SMAJ51CA; D_SMA; Manufacturer# SMAJ60CA-13-F; LCSC Part # C135003
J20: BDC_00_SELECTOR; PinHeader_1x03_P2.54mm_Vertical; Manufacturer# PZ2.54-1*3; LCSC Part # C5360899
J21: BDC_01_SELECTOR; PinHeader_1x03_P2.54mm_Vertical; Manufacturer# PZ2.54-1*3; LCSC Part # C5360899
L25, L26: 8.2 uH; SRR1210-8R2Y; Manufacturer# SRR1210-8R2Y
L27, L28, L29, L30: BBUP00100505330Y00; L_0402_1005Metric; Manufacturer# BLM15AX100SN1D; LCSC Part # C668299
R77, R78: 49.9K; R_0603_1608Metric; Tolerance 1%; Manufacturer# RC0603FR-0749K9L
R79, R81: 100K; R_0603_1608Metric; Tolerance 1%; Manufacturer# RT0603FRE07100KL; LCSC Part # C728638
R80, R82: 9.09K; R_0603_1608Metric; Tolerance 1%; Manufacturer# RC0603FR-079K09L; LCSC Part # C185301
R83, R84: 0.11R; R_2512_6332Metric; Tolerance 1%; Manufacturer# YHR2512SE2WR110F4; LCSC Part # C46595965
R85, R86, R87, R88: 150R; R_0603_1608Metric; Tolerance 1%; Manufacturer# RC0603FR-07150RL; LCSC Part # C114608
U6, U7: LV14360PDDAR; Manufacturer# LV14360PDDAR; LCSC Part # C2864599
U8, U9: DRV8870DDA; Manufacturer# DRV8870DDAR; LCSC Part # C86590

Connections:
+3.3V: U8.4 (VREF), U9.4 (VREF); also elsewhere on the board
+24V: J20.2, J21.2; also elsewhere on the board
/9V_brushless_motor_drivers/BDC_01_OUT1: C75.1, D30.1 (A1), L29.2; also elsewhere on the board
/9V_brushless_motor_drivers/BDC_01_OUT2: C77.1, D30.2 (A2), L27.2; also elsewhere on the board
/9V_brushless_motor_drivers/BDC_02_OUT1: C76.1, D31.1 (A1), L30.2; also elsewhere on the board
/9V_brushless_motor_drivers/BDC_02_OUT2: C78.1, D31.2 (A2), L28.2; also elsewhere on the board
/GPIO_02 (I2C_01_SDA): U8.3 (IN1); also elsewhere on the board
/GPIO_03 (I2C_01_SCL): U8.2 (IN2); also elsewhere on the board
/GPIO_09 (SPIO_MISO): U9.3 (IN1); also elsewhere on the board
/GPIO_10 (SPIO_MOSI): U9.2 (IN2); also elsewhere on the board
GND: C59.1, C60.2, C61.1, C62.2, C63.1, C64.1, C65.1, C66.1, C69.2, C70.2, C71.1, C72.1, C73.1, C74.1, D26.2 (A), D27.2 (A), R77.2, R78.2, R80.1, R82.1, R83.2, R84.2, R85.2, R86.2, R87.2, R88.2, U6.7 (GND), U6.9 (PAD), U7.7 (GND), U7.9 (PAD), U8.1 (GND), U8.9 (GND), U9.1 (GND), U9.9 (GND); also elsewhere on the board
unnamed: C75.2, R85.1
unnamed: C76.2, R86.1
unnamed: C77.2, R87.1
unnamed: C78.2, R88.1
unnamed: C67.1, D26.1 (K), L25.1, U6.8 (SW)
unnamed: C68.1, D27.1 (K), L26.1, U7.8 (SW)
unnamed: C59.2, C60.1, C63.2, C65.2, J20.1, U6.2 (VIN), U6.3 (EN)
unnamed: C69.1, C71.2, C73.2, J20.3, L25.2, R79.2, U8.5 (VM)
unnamed: C61.2, C62.1, C64.2, C66.2, J21.1, U7.2 (VIN), U7.3 (EN)
unnamed: C70.1, C72.2, C74.2, J21.3, L26.2, R81.2, U9.5 (VM)
unnamed: C67.2, U6.1 (BOOT)
unnamed: R79.1, R80.2, U6.5 (FB)
unnamed: R77.1, U6.4 (RT_SYNC)
unnamed: C68.2, U7.1 (BOOT)
unnamed: R81.1, R82.2, U7.5 (FB)
unnamed: R78.1, U7.4 (RT_SYNC)
unnamed: R83.1, U8.7 (ISEN)
unnamed: L27.1, U8.6 (OUT1)
unnamed: L29.1, U8.8 (OUT2)
unnamed: R84.1, U9.7 (ISEN)
unnamed: L28.1, U9.6 (OUT1)
unnamed: L30.1, U9.8 (OUT2)

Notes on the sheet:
- RC Snubber: 150Ω + 100pF - TVS: SMAJ51CA 400W - Common Mode Choke

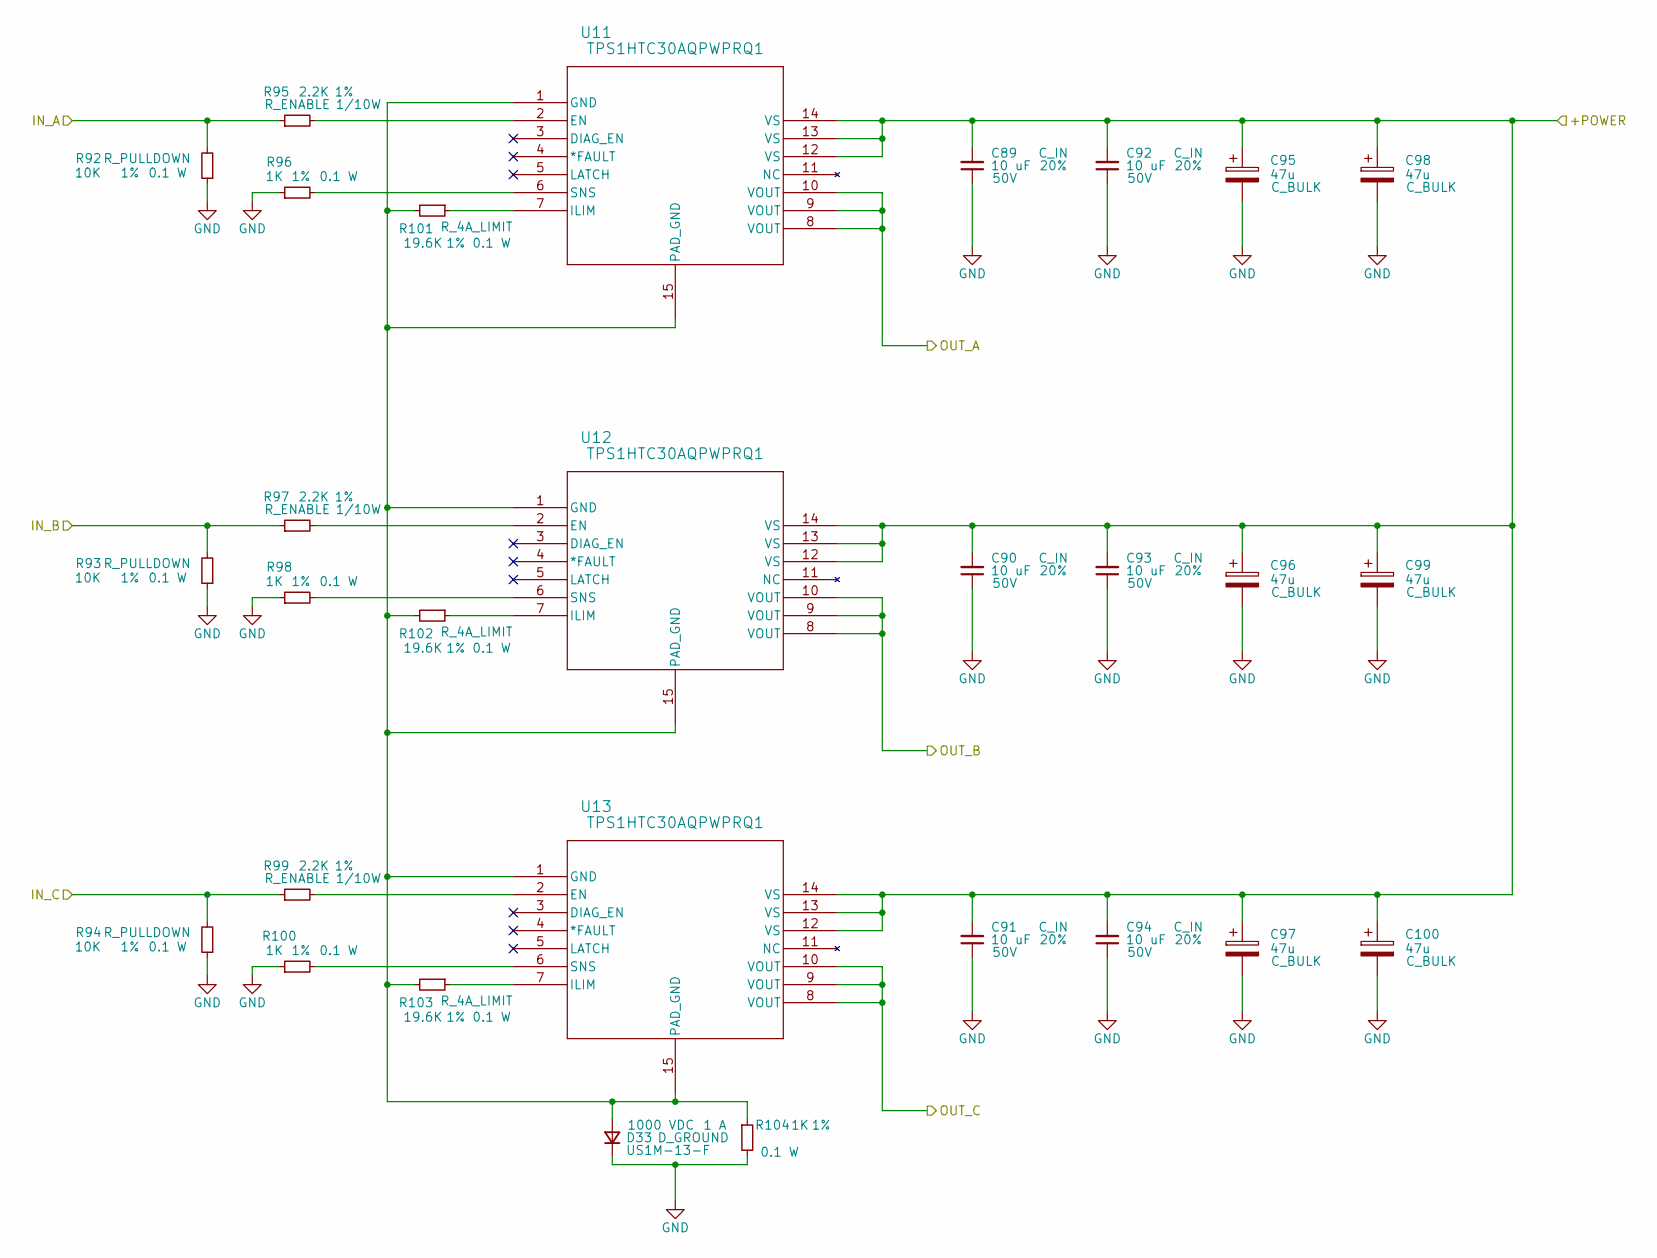
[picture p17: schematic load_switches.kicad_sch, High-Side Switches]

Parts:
C89, C90, C91, C92, C93, C94: 10 uF; C_1206_3216Metric; Tolerance 20%; Max Voltage 50V; Manufacturer# CL31A106MBHNNNE; LCSC Part # C96600
C95, C96, C97, C98, C99, C100: 47u; CP_Elec_6.3x5.9; Manufacturer# 35SVPK47M; LCSC Part # C264034
D33: US1M-13-F; D_SMA; Tolerance NULL; Manufacturer# US1M-13-F; LCSC Part # C99333
R92, R93, R94: 10K; R_0603_1608Metric; Tolerance 1%; Manufacturer# RC0603BR-0710KL; LCSC Part # C98220
R95, R97, R99: 2.2K; R_0603_1608Metric; Tolerance 1%; Manufacturer# RC0603FR-072K2L; LCSC Part # C114662
R96, R98, R100, R104: 1K; R_0603_1608Metric; Tolerance 1%; Manufacturer# RC0603FR-071KL; LCSC Part # C22548
R101, R102, R103: 19.6K; R_0603_1608Metric; Tolerance 1%; Manufacturer# RC0603FR-0719K6L; LCSC Part # C245925
U11, U12, U13: TPS1HTC30AQPWPRQ1; TPS1HTC30-Q1; Manufacturer# TPS1HTC30AQPWPRQ1; LCSC Part # C22414694

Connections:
/GPIO_07 (SPI_0_CE1): R93.2, R97.1; also elsewhere on the board
/GPIO_08 (SPI_0_CE0): R94.2, R99.1; also elsewhere on the board
/GPIO_11 (SPIO_SCLK): R92.2, R95.1; also elsewhere on the board
/load_switches/+POWER: C89.2, C90.2, C91.2, C92.2, C93.2, C94.2, C95.1, C96.1, C97.1, C98.1, C99.1, C100.1, U11.12 (VS), U11.13 (VS), U11.14 (VS), U12.12 (VS), U12.13 (VS), U12.14 (VS), U13.12 (VS), U13.13 (VS), U13.14 (VS); also elsewhere on the board
/load_switches/OUT_A: U11.8 (VOUT), U11.9 (VOUT), U11.10 (VOUT); also elsewhere on the board
/load_switches/OUT_B: U12.8 (VOUT), U12.9 (VOUT), U12.10 (VOUT); also elsewhere on the board
/load_switches/OUT_C: U13.8 (VOUT), U13.9 (VOUT), U13.10 (VOUT); also elsewhere on the board
GND: C89.1, C90.1, C91.1, C92.1, C93.1, C94.1, C95.2, C96.2, C97.2, C98.2, C99.2, C100.2, D33.1 (K), R92.1, R93.1, R94.1, R96.1, R98.1, R100.1, R104.2; also elsewhere on the board
unnamed: D33.2 (A), R101.2, R102.2, R103.2, R104.1, U11.1 (GND), U11.15 (PAD_GND), U12.1 (GND), U12.15 (PAD_GND), U13.1 (GND), U13.15 (PAD_GND)
unnamed: R95.2, U11.2 (EN)
unnamed: R101.1, U11.7 (ILIM)
unnamed: R96.2, U11.6 (SNS)
unnamed: R97.2, U12.2 (EN)
unnamed: R102.1, U12.7 (ILIM)
unnamed: R98.2, U12.6 (SNS)
unnamed: R99.2, U13.2 (EN)
unnamed: R103.1, U13.7 (ILIM)
unnamed: R100.2, U13.6 (SNS)

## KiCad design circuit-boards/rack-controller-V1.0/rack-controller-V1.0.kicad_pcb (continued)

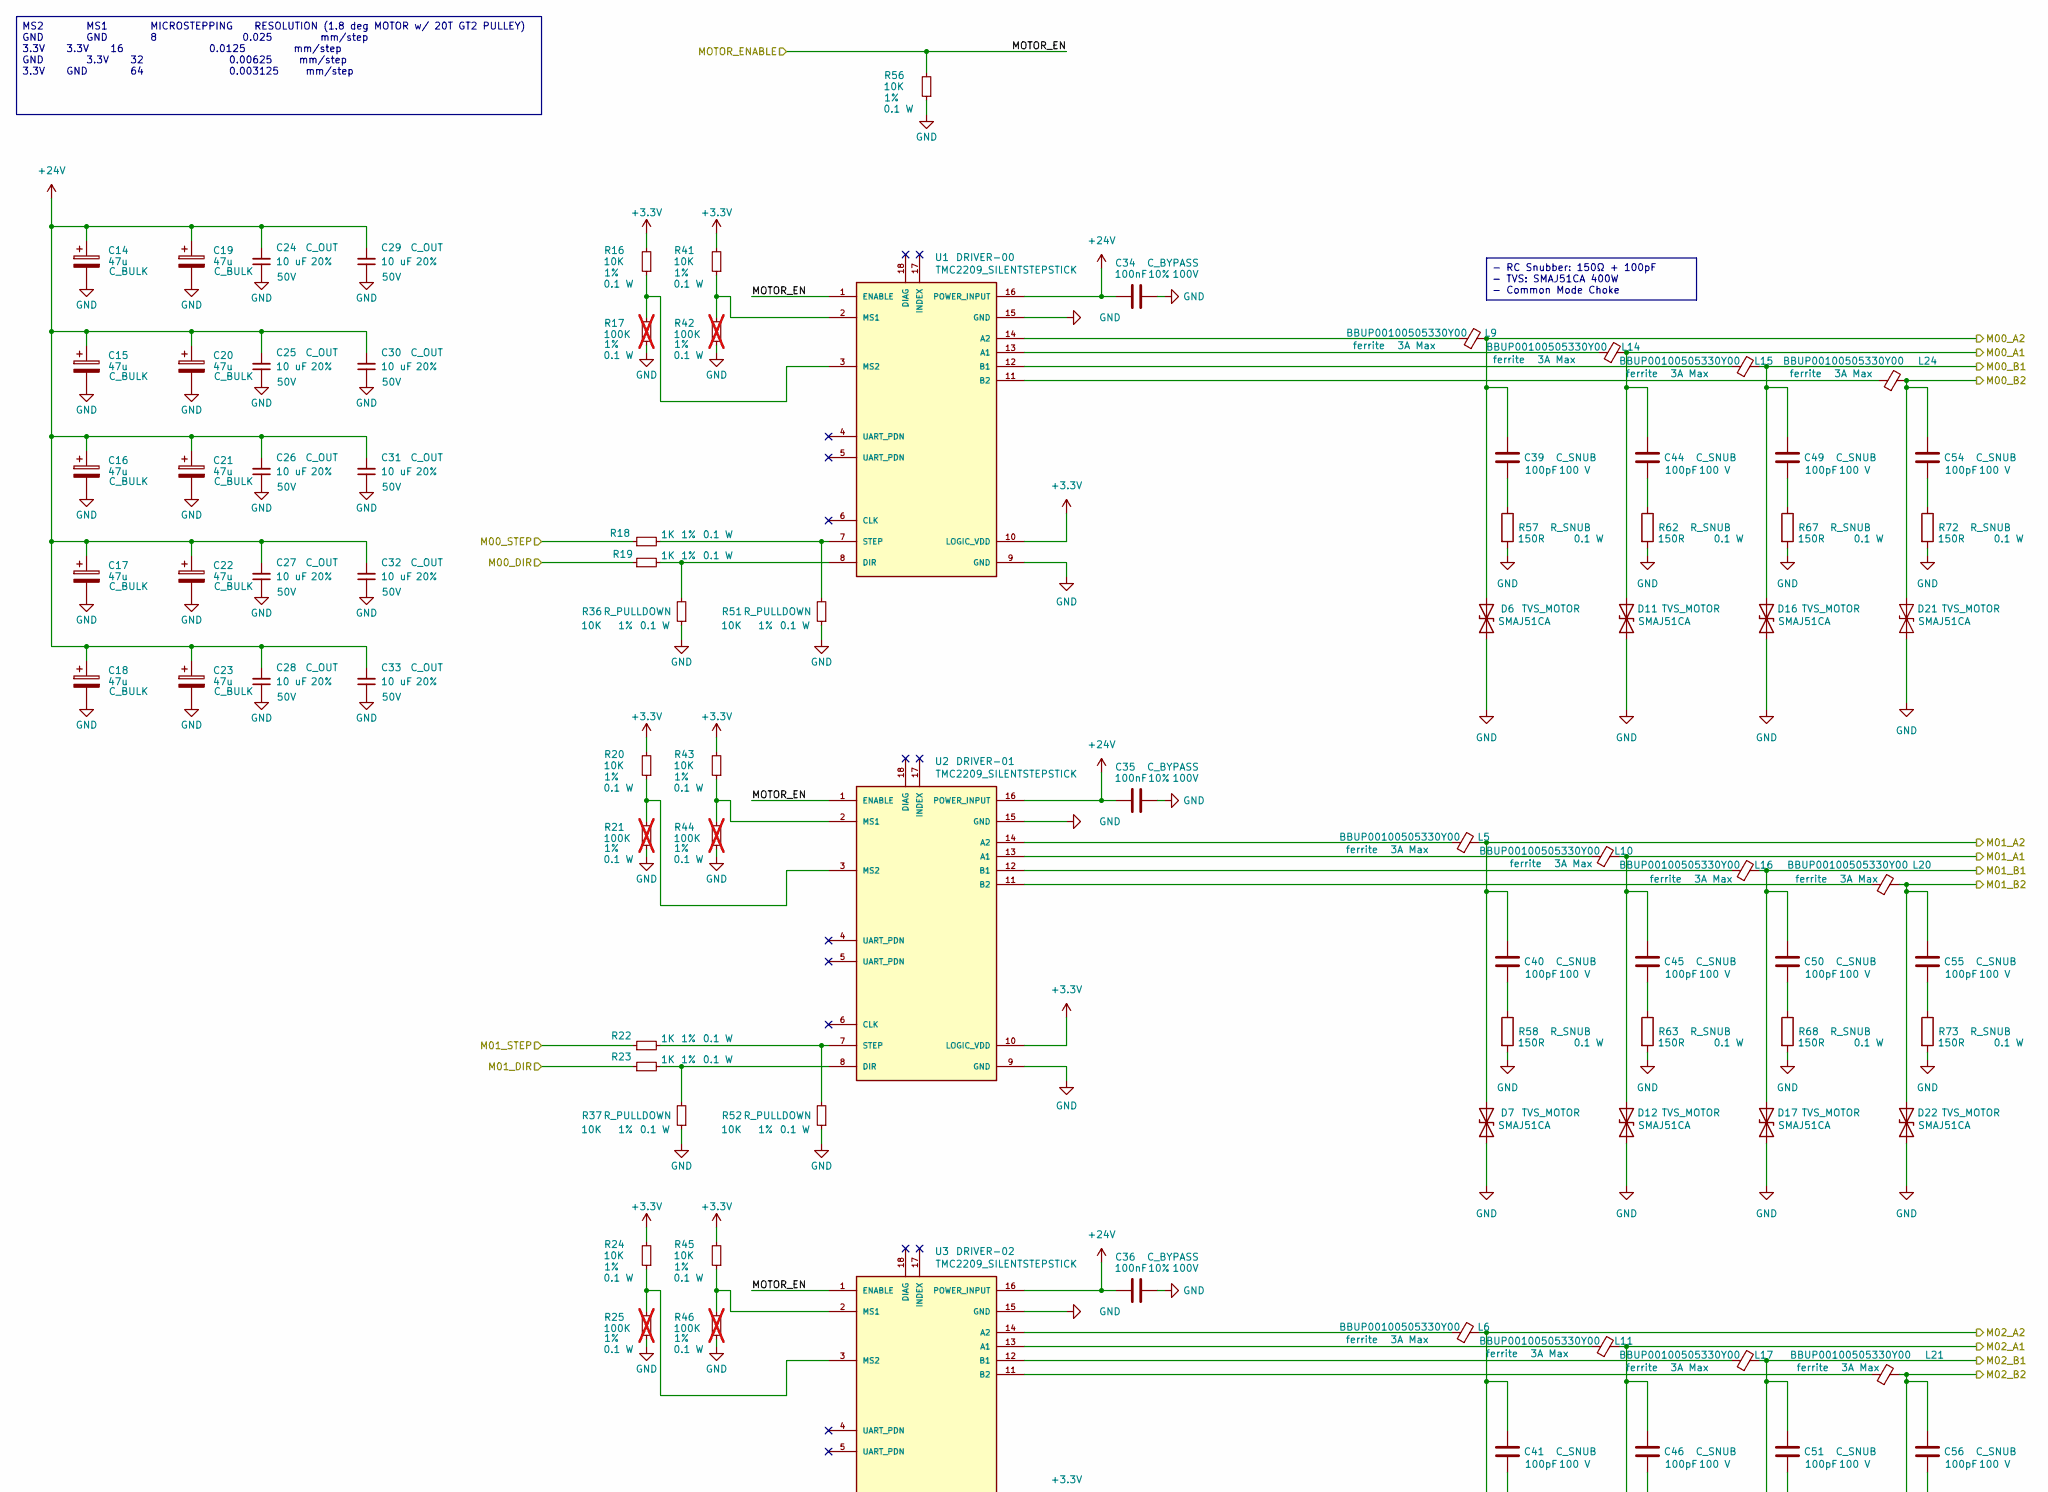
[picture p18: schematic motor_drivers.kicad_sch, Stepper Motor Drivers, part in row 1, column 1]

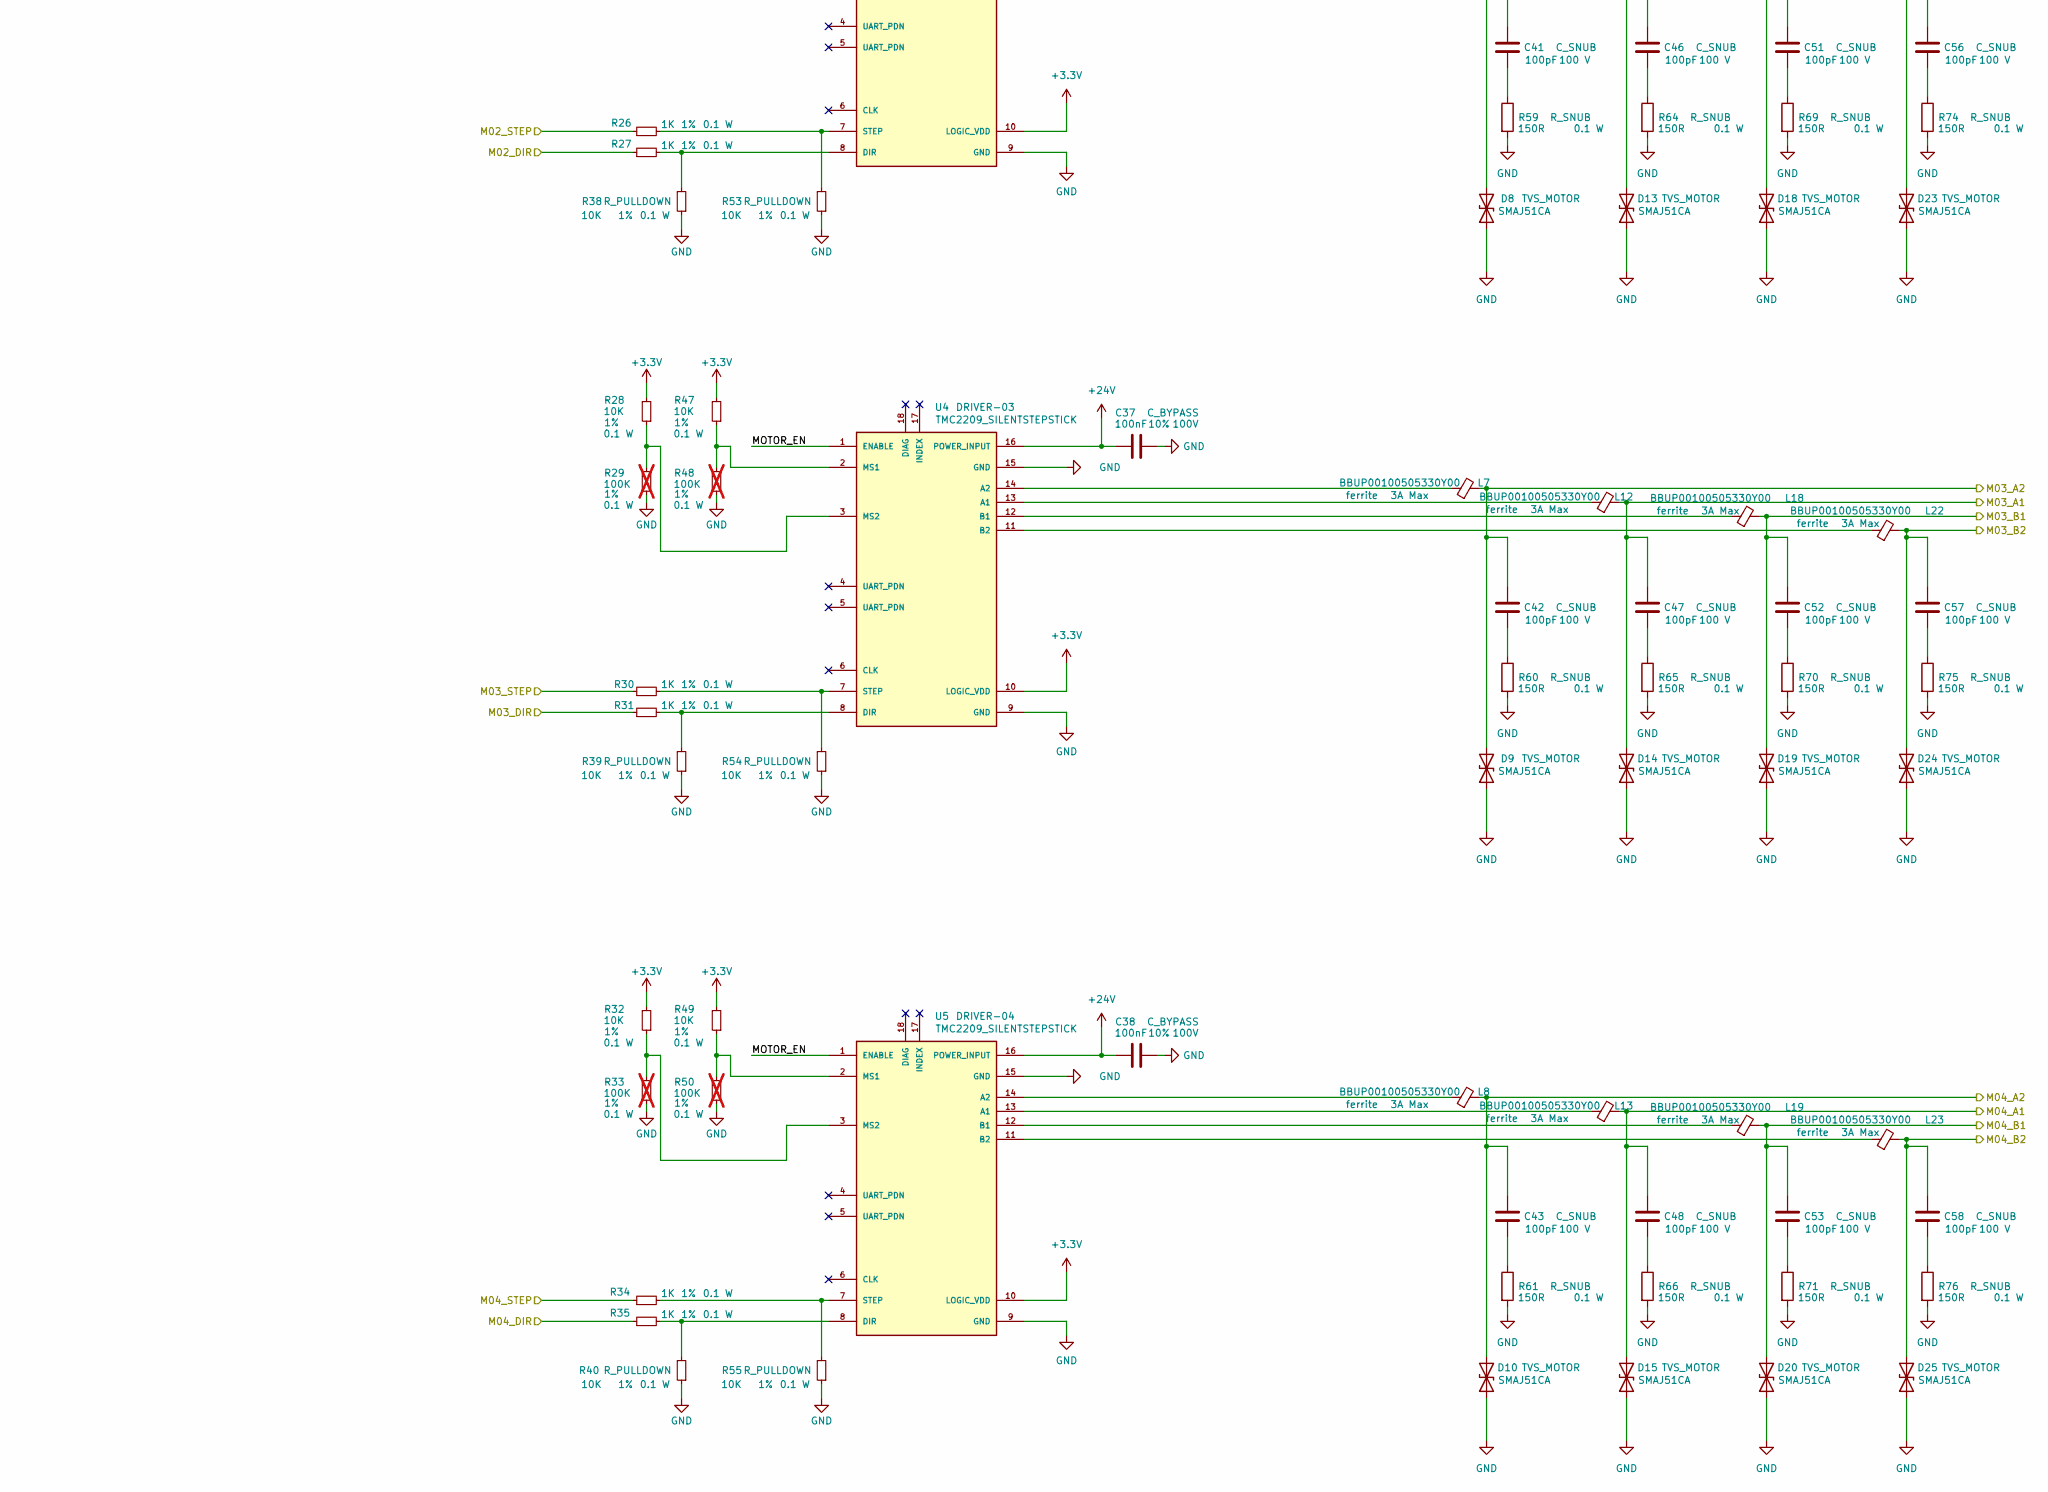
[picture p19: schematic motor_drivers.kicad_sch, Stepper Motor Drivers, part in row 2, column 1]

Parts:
C14, C15, C16, C17, C18, C19, C20, C21, C22, C23: 47u; CP_Elec_6.3x5.9; Manufacturer# 35SVPK47M; LCSC Part # C264034
C24, C25, C26, C27, C28, C29, C30, C31, C32, C33: 10 uF; C_1206_3216Metric; Tolerance 20%; Max Voltage 50V; Manufacturer# CL31A106MBHNNNE; LCSC Part # C96600
C34, C35, C36, C37, C38: 100nF; C_0603_1608Metric; Voltage 100V; Tolerance 10%; Manufacturer# CC0603KRX7R0BB104; LCSC Part # C113803
C39, C40, C41, C42, C43, C44, C45, C46, C47, C48, C49, C50, C51, C52, C53, C54, C55, C56, C57, C58: 100pF; C_0402_1005Metric; Voltage 100 V; Manufacturer# CC0402JRNPO0BN101; LCSC Part # C576700
D6, D7, D8, D9, D10, D11, D12, D13, D14, D15, D16, D17, D18, D19, D20, D21, D22, D23, D24, D25: SMAJ51CA; D_SMA; Manufacturer# SMAJ60CA-13-F; LCSC Part # C135003
L5, L6, L7, L8, L9, L10, L11, L12, L13, L14, L15, L16, L17, L18, L19, L20, L21, L22, L23, L24: BBUP00100505330Y00; L_0402_1005Metric; Manufacturer# BLM15AX100SN1D; LCSC Part # C668299
R16, R20, R24, R28, R32, R36, R37, R38, R39, R40, R41, R43, R45, R47, R49, R51, R52, R53, R54, R55, R56: 10K; R_0603_1608Metric; Tolerance 1%; Manufacturer# RC0603BR-0710KL; LCSC Part # C98220
R17, R21, R25, R29, R33, R42, R44, R46, R48, R50: 100K; R_0603_1608Metric; Tolerance 1%; Manufacturer# RT0603FRE07100KL; LCSC Part # C728638; not fitted
R18, R19, R22, R23, R26, R27, R30, R31, R34, R35: 1K; R_0603_1608Metric; Tolerance 1%; Manufacturer# RC0603FR-071KL; LCSC Part # C22548
R57, R58, R59, R60, R61, R62, R63, R64, R65, R66, R67, R68, R69, R70, R71, R72, R73, R74, R75, R76: 150R; R_0603_1608Metric; Tolerance 1%; Manufacturer# RC0603FR-07150RL; LCSC Part # C114608
U1, U2, U3, U4, U5: TMC2209_SILENTSTEPSTICK; BTT_TMC2209_V1.3; Manufacturer# TMC2209_V1.3; LCSC Part # NULL

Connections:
+3.3V: R16.2, R20.2, R24.2, R28.2, R32.2, R41.2, R43.2, R45.2, R47.2, R49.2, U1.10 (LOGIC_VDD), U2.10 (LOGIC_VDD), U3.10 (LOGIC_VDD), U4.10 (LOGIC_VDD), U5.10 (LOGIC_VDD); also elsewhere on the board
+24V: C14.1, C15.1, C16.1, C17.1, C18.1, C19.1, C20.1, C21.1, C22.1, C23.1, C24.2, C25.2, C26.2, C27.2, C28.2, C29.2, C30.2, C31.2, C32.2, C33.2, C34.2, C35.2, C36.2, C37.2, C38.2, U1.16 (POWER_INPUT), U2.16 (POWER_INPUT), U3.16 (POWER_INPUT), U4.16 (POWER_INPUT), U5.16 (POWER_INPUT); also elsewhere on the board
/GPIO_05: R18.1; also elsewhere on the board
/GPIO_06: R56.2, U1.1 (ENABLE), U2.1 (ENABLE), U3.1 (ENABLE), U4.1 (ENABLE), U5.1 (ENABLE); also elsewhere on the board
/GPIO_14 (UART_TX): R35.1; also elsewhere on the board
/GPIO_15 (UART_RX): R34.1; also elsewhere on the board
/GPIO_17: R30.1; also elsewhere on the board
/GPIO_18 (PCM_CLK): R31.1; also elsewhere on the board
/GPIO_22: R23.1; also elsewhere on the board
/GPIO_23: R26.1; also elsewhere on the board
/GPIO_24: R22.1; also elsewhere on the board
/GPIO_25: R19.1; also elsewhere on the board
/GPIO_27: R27.1; also elsewhere on the board
/stepper_motor_drivers/M00_A1: C44.1, D11.2 (A2), L14.2; also elsewhere on the board
/stepper_motor_drivers/M00_A2: C39.1, D6.2 (A2), L9.2; also elsewhere on the board
/stepper_motor_drivers/M00_B1: C49.1, D16.2 (A2), L15.2; also elsewhere on the board
/stepper_motor_drivers/M00_B2: C54.1, D21.2 (A2), L24.2; also elsewhere on the board
/stepper_motor_drivers/M01_A1: C45.1, D12.2 (A2), L10.2; also elsewhere on the board
/stepper_motor_drivers/M01_A2: C40.1, D7.2 (A2), L5.2; also elsewhere on the board
/stepper_motor_drivers/M01_B1: C50.1, D17.2 (A2), L16.2; also elsewhere on the board
/stepper_motor_drivers/M01_B2: C55.1, D22.2 (A2), L20.2; also elsewhere on the board
/stepper_motor_drivers/M02_A1: C46.1, D13.2 (A2), L11.2; also elsewhere on the board
/stepper_motor_drivers/M02_A2: C41.1, D8.2 (A2), L6.2; also elsewhere on the board
/stepper_motor_drivers/M02_B1: C51.1, D18.2 (A2), L17.2; also elsewhere on the board
/stepper_motor_drivers/M02_B2: C56.1, D23.2 (A2), L21.2; also elsewhere on the board
/stepper_motor_drivers/M03_A1: C47.1, D14.2 (A2), L12.2; also elsewhere on the board
/stepper_motor_drivers/M03_A2: C42.1, D9.2 (A2), L7.2; also elsewhere on the board
/stepper_motor_drivers/M03_B1: C52.1, D19.2 (A2), L18.2; also elsewhere on the board
/stepper_motor_drivers/M03_B2: C57.1, D24.2 (A2), L22.2; also elsewhere on the board
/stepper_motor_drivers/M04_A1: C48.1, D15.2 (A2), L13.2; also elsewhere on the board
/stepper_motor_drivers/M04_A2: C43.1, D10.2 (A2), L8.2; also elsewhere on the board
/stepper_motor_drivers/M04_B1: C53.1, D20.2 (A2), L19.2; also elsewhere on the board
/stepper_motor_drivers/M04_B2: C58.1, D25.2 (A2), L23.2; also elsewhere on the board
GND: C14.2, C15.2, C16.2, C17.2, C18.2, C19.2, C20.2, C21.2, C22.2, C23.2, C24.1, C25.1, C26.1, C27.1, C28.1, C29.1, C30.1, C31.1, C32.1, C33.1, C34.1, C35.1, C36.1, C37.1, C38.1, D6.1 (A1), D7.1 (A1), D8.1 (A1), D9.1 (A1), D10.1 (A1), D11.1 (A1), D12.1 (A1), D13.1 (A1), D14.1 (A1), D15.1 (A1), D16.1 (A1), D17.1 (A1), D18.1 (A1), D19.1 (A1), D20.1 (A1), D21.1 (A1), D22.1 (A1), D23.1 (A1), D24.1 (A1), D25.1 (A1), R17.1, R21.1, R25.1, R29.1, R33.1, R36.1, R37.1, R38.1, R39.1, R40.1, R42.1, R44.1, R46.1, R48.1, R50.1, R51.1, R52.1, R53.1, R54.1, R55.1, R56.1, R57.2, R58.2, R59.2, R60.2, R61.2, R62.2, R63.2, R64.2, R65.2, R66.2, R67.2, R68.2, R69.2, R70.2, R71.2, R72.2, R73.2, R74.2, R75.2, R76.2, U1.9 (GND), U1.15 (GND), U2.9 (GND), U2.15 (GND), U3.9 (GND), U3.15 (GND), U4.9 (GND), U4.15 (GND), U5.9 (GND), U5.15 (GND); also elsewhere on the board
unnamed: C39.2, R57.1
unnamed: C40.2, R58.1
unnamed: C41.2, R59.1
unnamed: C42.2, R60.1
unnamed: C43.2, R61.1
unnamed: C44.2, R62.1
unnamed: C45.2, R63.1
unnamed: C46.2, R64.1
unnamed: C47.2, R65.1
unnamed: C48.2, R66.1
unnamed: C49.2, R67.1
unnamed: C50.2, R68.1
unnamed: C51.2, R69.1
unnamed: C52.2, R70.1
unnamed: C53.2, R71.1
unnamed: C54.2, R72.1
unnamed: C55.2, R73.1
unnamed: C56.2, R74.1
unnamed: C57.2, R75.1
unnamed: C58.2, R76.1
unnamed: L14.1, U1.13 (A1)
unnamed: L9.1, U1.14 (A2)
unnamed: L15.1, U1.12 (B1)
unnamed: L24.1, U1.11 (B2)
unnamed: R19.2, R36.2, U1.8 (DIR)
unnamed: R41.1, R42.2, U1.2 (MS1)
unnamed: R16.1, R17.2, U1.3 (MS2)
unnamed: R18.2, R51.2, U1.7 (STEP)
unnamed: L10.1, U2.13 (A1)
unnamed: L5.1, U2.14 (A2)
unnamed: L16.1, U2.12 (B1)
unnamed: L20.1, U2.11 (B2)
unnamed: R23.2, R37.2, U2.8 (DIR)
unnamed: R43.1, R44.2, U2.2 (MS1)
unnamed: R20.1, R21.2, U2.3 (MS2)
unnamed: R22.2, R52.2, U2.7 (STEP)
unnamed: L11.1, U3.13 (A1)
unnamed: L6.1, U3.14 (A2)
unnamed: L17.1, U3.12 (B1)
unnamed: L21.1, U3.11 (B2)
unnamed: R27.2, R38.2, U3.8 (DIR)
unnamed: R45.1, R46.2, U3.2 (MS1)
unnamed: R24.1, R25.2, U3.3 (MS2)
unnamed: R26.2, R53.2, U3.7 (STEP)
unnamed: L12.1, U4.13 (A1)
unnamed: L7.1, U4.14 (A2)
unnamed: L18.1, U4.12 (B1)
unnamed: L22.1, U4.11 (B2)
unnamed: R31.2, R39.2, U4.8 (DIR)
unnamed: R47.1, R48.2, U4.2 (MS1)
unnamed: R28.1, R29.2, U4.3 (MS2)
unnamed: R30.2, R54.2, U4.7 (STEP)
unnamed: L13.1, U5.13 (A1)
unnamed: L8.1, U5.14 (A2)
unnamed: L19.1, U5.12 (B1)
unnamed: L23.1, U5.11 (B2)
unnamed: R35.2, R40.2, U5.8 (DIR)
unnamed: R49.1, R50.2, U5.2 (MS1)
unnamed: R32.1, R33.2, U5.3 (MS2)
unnamed: R34.2, R55.2, U5.7 (STEP)

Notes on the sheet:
- RC Snubber: 150Ω + 100pF - TVS: SMAJ51CA 400W - Common Mode Choke
MS2 MS1 MICROSTEPPING RESOLUTION (1.8 deg MOTOR w/ 20T GT2 PULLEY) GND GND 8 0.025 mm/step 3.3V 3.3V 16 0.0125 mm/step GND 3.3V 32 0.00625 mm/step 3.3V GND 64 0.003125 mm/step

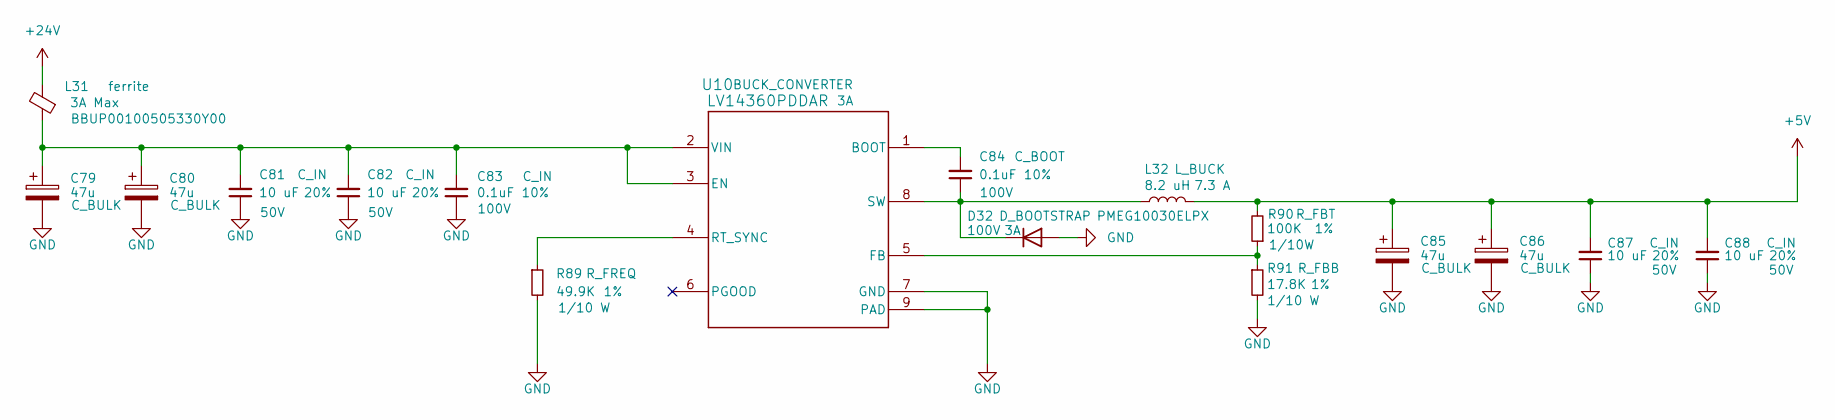
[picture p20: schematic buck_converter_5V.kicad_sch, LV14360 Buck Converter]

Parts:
C79, C80, C85, C86: 47u; CP_Elec_6.3x5.9; Manufacturer# 35SVPK47M; LCSC Part # C264034
C81, C82, C87, C88: 10 uF; C_1206_3216Metric; Tolerance 20%; Max Voltage 50V; Manufacturer# CL31A106MBHNNNE; LCSC Part # C96600
C83, C84: 0.1uF; C_0603_1608Metric; Tolerance 10%; Max Voltage 100V; Manufacturer# CC0603KRX7R0BB104; LCSC Part # C113803
D32: PMEG10030ELPX; D_SOD-128; Max Voltage 100V; Manufacturer# PMEG10030ELPX; LCSC Part # C5260346
L31: BBUP00100505330Y00; L_0402_1005Metric; Manufacturer# BLM15AX100SN1D; LCSC Part # C668299
L32: 8.2 uH; SRR1210-8R2Y; Manufacturer# SRR1210-8R2Y
R89: 49.9K; R_0603_1608Metric; Tolerance 1%; Manufacturer# RC0603FR-0749K9L
R90: 100K; R_0603_1608Metric; Tolerance 1%; Manufacturer# RT0603FRE07100KL; LCSC Part # C728638
R91: 17.8K; R_0603_1608Metric; Tolerance 1%; Manufacturer# RC0603FR-0717K8L; LCSC Part # C185364
U10: LV14360PDDAR; Manufacturer# LV14360PDDAR; LCSC Part # C2864599

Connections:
+5V: C85.1, C86.1, C87.2, C88.2, L32.2, R90.2; also elsewhere on the board
+24V: L31.2; also elsewhere on the board
GND: C79.2, C80.2, C81.1, C82.1, C83.1, C85.2, C86.2, C87.1, C88.1, D32.2 (A), R89.2, R91.2, U10.7 (GND), U10.9 (PAD); also elsewhere on the board
unnamed: C84.1, D32.1 (K), L32.1, U10.8 (SW)
unnamed: C84.2, U10.1 (BOOT)
unnamed: C79.1, C80.1, C81.2, C82.2, C83.2, L31.1, U10.2 (VIN), U10.3 (EN)
unnamed: R90.1, R91.1, U10.5 (FB)
unnamed: R89.1, U10.4 (RT_SYNC)

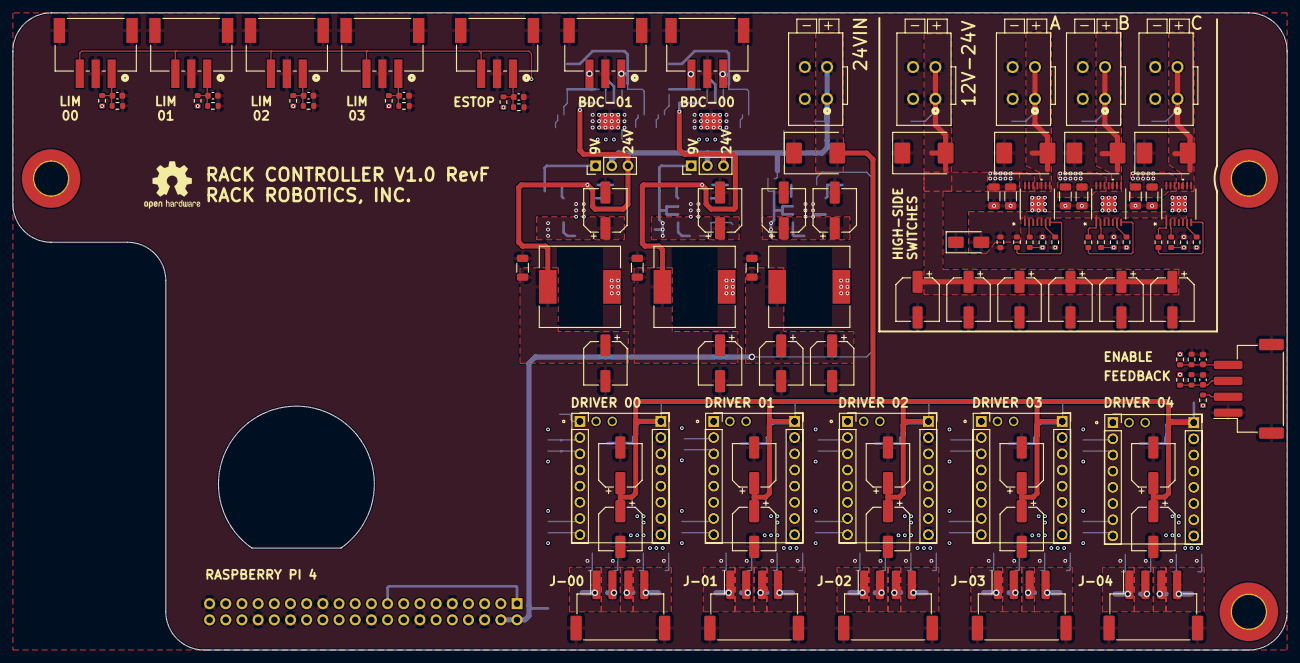
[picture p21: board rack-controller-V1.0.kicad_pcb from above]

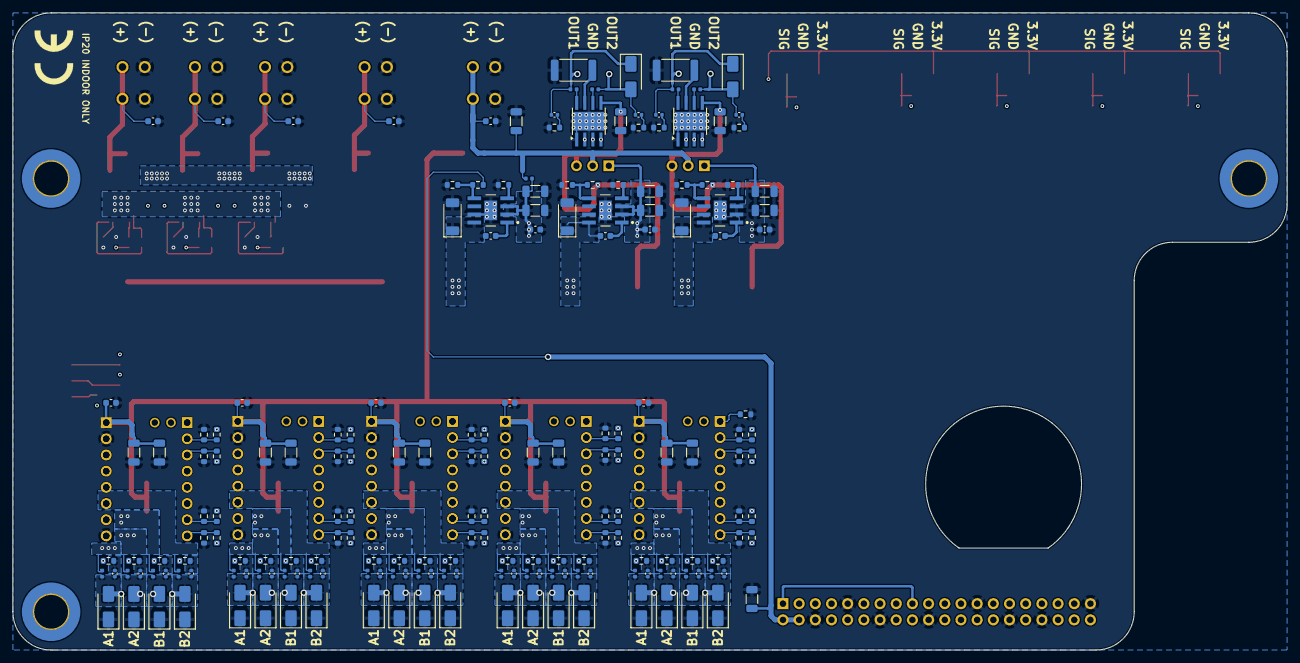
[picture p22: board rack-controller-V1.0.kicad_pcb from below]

Board: 6 copper layers, 200.0 x 100.0 mm, 311 parts (191 on the bottom side), 163 nets.

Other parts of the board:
HDR1, HDR1#2, HDR2, HDR2#2, HDR3, HDR4, HDR5, HDR6, HDR7, HDR8: PinSocket_1x08_P2.54mm_Vertical
RP4: Raspberry_Pi; raspberrypi-outline

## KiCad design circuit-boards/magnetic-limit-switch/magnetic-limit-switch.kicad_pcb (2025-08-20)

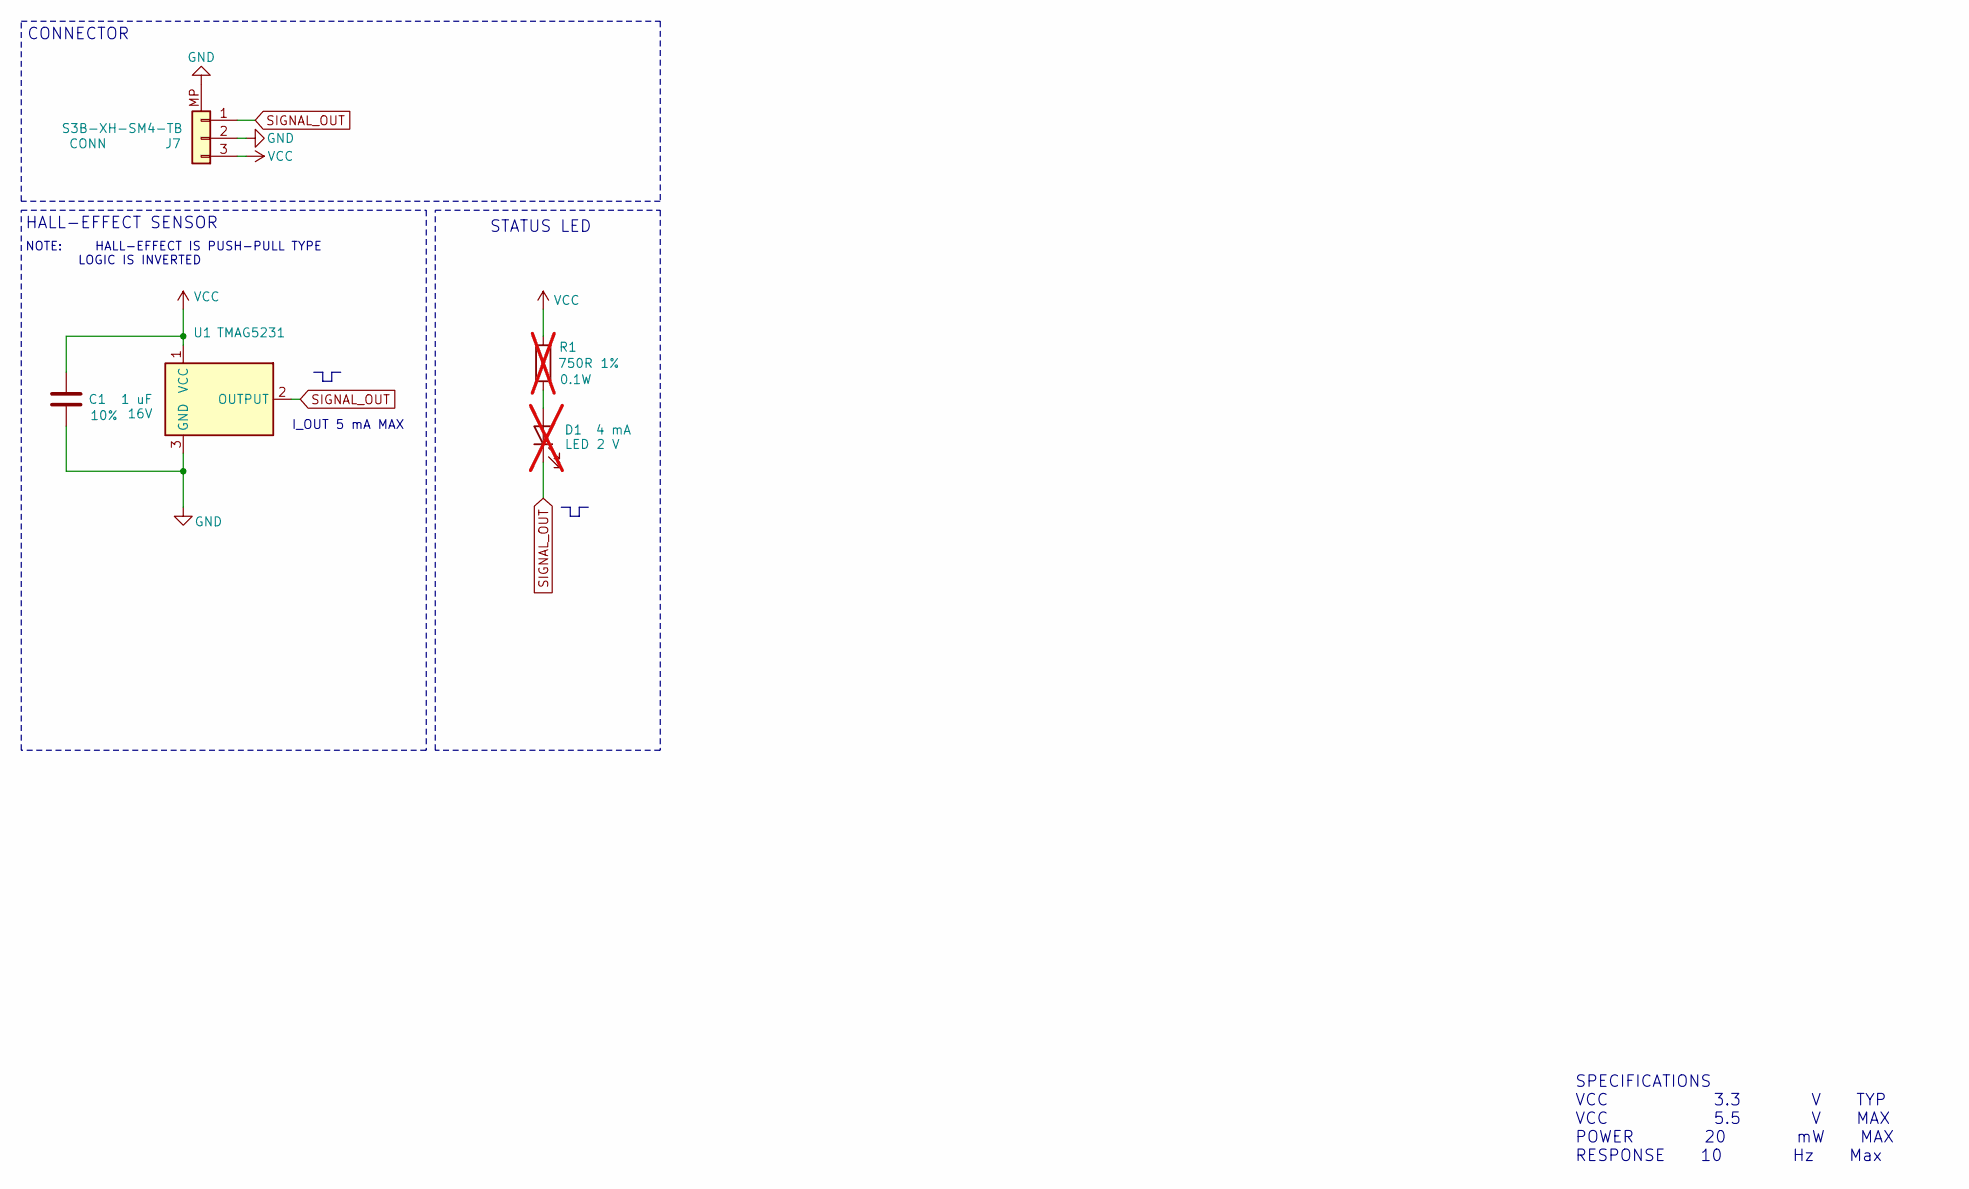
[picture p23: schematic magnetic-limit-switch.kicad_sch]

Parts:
C1: 1 uF; C_0603_1608Metric; Tolerance 10%; Manufacterer# CC0603KRX7R7BB105; LCSC Part # C106248
D1: LED; LED_0603_1608Metric; Manufacterer# LTST-C193KFKT-5A; LCSC Part # C284922; not fitted
J7: S3B-XH-SM4-TB; JST_XH_S3B-XH-SM4-TB_1x03-1MP_P2.50mm_Horizontal; Manufacterer# S3B-XH-SM4-TB; LCSC Part # C161860
R1: 750R; R_0603_1608Metric; Tolerance 1%; Manufacterer# RC0603FR-07750RL; LCSC Part # C114635; not fitted
U1: TMAG5231; SOT-23-3; Manufacterer# TMAG5231A2DQDBZR; LCSC Part # C17378950

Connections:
GND: C1.1, J7.2, J7.MP, U1.3 (GND)
unnamed: D1.2 (A), R1.1
SIGNAL_OUT: D1.1 (K), J7.1, U1.2 (OUTPUT)
VCC: C1.2, J7.3, R1.2, U1.1 (VCC)

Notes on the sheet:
NOTE: HALL-EFFECT IS PUSH-PULL TYPE LOGIC IS INVERTED
CONNECTOR
HALL-EFFECT SENSOR
STATUS LED
SPECIFICATIONS VCC 3.3 V TYP VCC 5.5 V MAX POWER 20 mW MAX RESPONSE 10 Hz Max
I_OUT 5 mA MAX

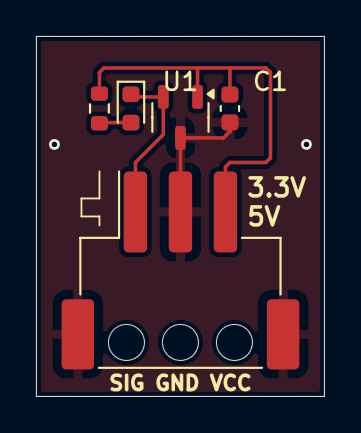
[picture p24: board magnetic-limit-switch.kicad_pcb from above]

Board: 2 copper layers, 16.0 x 20.0 mm, 5 parts (0 on the bottom side), 4 nets.

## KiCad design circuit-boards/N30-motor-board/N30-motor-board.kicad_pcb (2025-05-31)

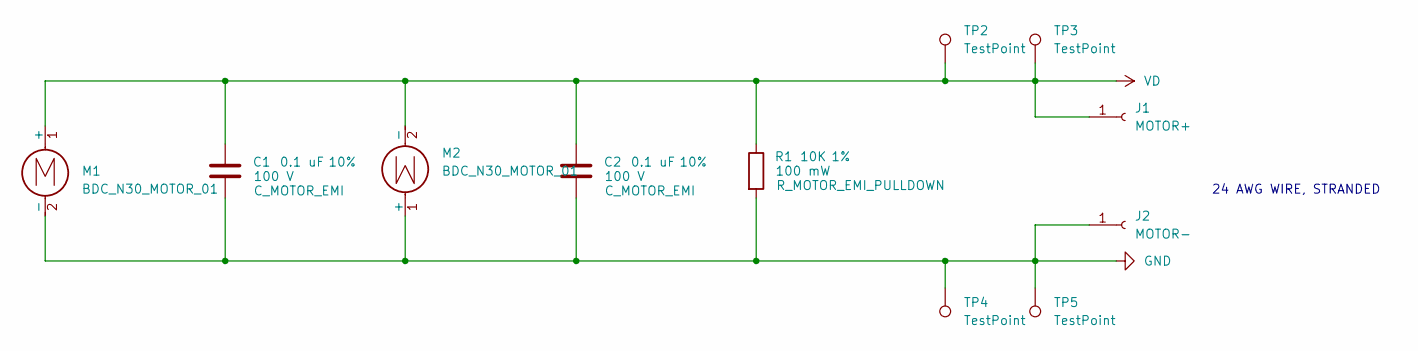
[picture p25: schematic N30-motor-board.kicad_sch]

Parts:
C1, C2: 0.1 uF; C_0603_1608Metric; Max Voltage 100 V; Tolerance 10%; Manufacturer# CC0603KRX7R0BB104; LCSC Part # C113803
J1: MOTOR+; SolderWire-0.25sqmm_1x01_D0.65mm_OD1.7mm
J2: MOTOR-; SolderWire-0.25sqmm_1x01_D0.65mm_OD1.7mm
M1, M2: BDC_N30_MOTOR_01; N30_MOTOR_TH
R1: 10K; R_0603_1608Metric; Tolerance 1%; Manufacturer# RC0603FR-0710KL; LCSC Part # C98220
TP2, TP3, TP4, TP5: TestPoint; TestPoint_Pad_2.0x2.0mm

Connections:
GND: C1.2, C2.2, J2.1, M1.2 (-), M2.1 (+), R1.2, TP4.1, TP5.1
VD: C1.1, C2.1, J1.1, M1.1 (+), M2.2 (-), R1.1, TP2.1, TP3.1

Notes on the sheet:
24 AWG WIRE, STRANDED

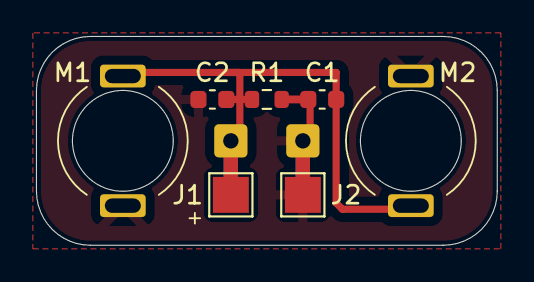
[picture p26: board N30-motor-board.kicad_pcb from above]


Board: 2 copper layers, 25.6 x 11.6 mm, 11 parts (2 on the bottom side), 2 nets.

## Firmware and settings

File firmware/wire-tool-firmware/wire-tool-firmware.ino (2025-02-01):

/*
 * Rack Robotics, Inc.
 * Wire Tool Firmware - Velocity Control Implementation
 * For use with Rarduino-Pico Plugin by EarlePhilhower
 * 
 * Dependencies: Wire.h (built-in)
 * Hardware: RP2040, AS5600, DRV8871, ACS723
 * 
 */

#include <Wire.h>

// Pin Definitions
const int I2C_SDA                             = 4;                                                    // I2C Data for AS5600 encoder
const int I2C_SCL                             = 5;                                                    // I2C Clock for AS5600 encoder
const int TOP_MOTOR_DRV8871_IN1               = 19;                                                   // Motor driver IN1 for top tool motor
const int TOP_MOTOR_DRV8871_IN2               = 18;                                                   // Motor driver IN2 for top tool motor
const int BOTTOM_MOTOR_DRV8871_IN1            = 17;                                                   // Motor driver IN1 for bottom tool motor
const int BOTTOM_MOTOR_DRV8871_IN2            = 16;                                                   // Motor driver IN2 for bottom tool motor
const int STATUS_LED                          = 25;                                                   // Status LED on Pico
const int TOP_MOTOR_ACS723                    = 26;                                                   // Analog output of current sensor for top tool motor
const int BOTTOM_MOTOR_ACS723                 = 27;                                                   // Analog output of current sensor for bottom tool motor

// Safety Limits
const float MOTOR_VOLTAGE                     = 9;                                                    // Votage applied to motors from driver (volts DC)
const float MAX_TOP_MOTOR_POWER               = 9;                                                    // Maximum safe power for top motor (watts)
const float MAX_BOTTOM_MOTOR_POWER            = 9;                                                    // Maximum safe power for bottom motor (watts)
const float MAX_VELOCITY                      = 50.0;                                                 // Maximum allowed velocity in mm/s
const float MIN_VELOCITY                      = -50.0;                                                // Minimum allowed velocity in mm/s
const float MAX_CURRENT                       = 2.0;                                                  // Maximum allowed current in A
const float MIN_CURRENT                       = -2.0;                                                 // Minimum allowed current in A
const float MAX_VELOCITY_ERROR                = 20.0;                                                 // Maximum allowed velocity error in mm/s
const float MAX_CURRENT_ERROR                 = 500.0;                                                // Maximum allowed current error in mA
const int ERROR_CHECK_INTERVAL                = 100;                                                  // Check errors every 

// Command String Definitions
const String COMMAND_SET_TOP_MOTOR_PWM        = "WIRETOOL: SET_TOP_MOTOR_PWM";
const String COMMAND_SET_BOTTOM_MOTOR_PWM     = "WIRETOOL: SET_BOTTOM_MOTOR_PWM";
const String COMMAND_LOAD_WIRE                = "WIRETOOL: LOAD_WIRE";
const String COMMAND_EXIT_WIRE_LOADING        = "WIRETOOL: EXIT_WIRE_LOADING";
const String COMMAND_UNLOAD_WIRE              = "WIRETOOL: UNLOAD_WIRE";
const String COMMAND_CALIBRATE_WIRE_TENSION   = "WIRETOOL: CALIBRATE_WIRE_TENSION";
const String COMMAND_SET_WIRE_VELOCITY        = "WIRETOOL: SET_WIRE_VELOCITY";
const String COMMAND_SET_WIRE_TENSION         = "WIRETOOL: SET_WIRE_TENSION";
const String COMMAND_SET_KP                   = "WIRETOOL: SET_KP";
const String COMMAND_SET_KI                   = "WIRETOOL: SET_KI";
const String COMMAND_SET_KD                   = "WIRETOOL: SET_KD";
const String COMMAND_GET_PID                  = "WIRETOOL: GET_PID";
const String COMMAND_TEST_ERROR               = "WIRETOOL: TEST_ERROR";
const String COMMAND_RESET                    = "WIRETOOL: RESET";
const String COMMAND_GET_TELEMETRY            = "WIRETOOL: GET_TELEMETRY";

// Current sensor calibration
const int CALIBRATION_SAMPLES = 100;  // Number of samples to average for calibration
float topVoltageOffset = 0.0;         // Zero-current voltage offset for top motor
float bottomVoltageOffset = 0.0;      // Zero-current voltage offset for bottom motor
const float CURRENT_SENSOR_SENSITIVITY = 0.400;  // V/Amp

// Current sensing constants and variables
const int CURRENT_AVERAGE_SAMPLES = 10;  // Number of samples for moving average
float topCurrentReadings[CURRENT_AVERAGE_SAMPLES] = {0};    // Array for top motor current readings
float bottomCurrentReadings[CURRENT_AVERAGE_SAMPLES] = {0}; // Array for bottom motor current readings
int currentReadingIndex = 0;  // Index for circular buffer

// AS5600 Encoder Constants
const uint8_t AS5600_ADDR             = 0x36;                                                         // I2C address of AS5600 magnetic encoder
const uint8_t REG_RAW_ANGLE_H         = 0x0C;                                                         // High byte register for raw angle
const uint8_t REG_RAW_ANGLE_L         = 0x0D;                                                         // Low byte register for raw angle
const float WHEEL_DIAMETER            = 30.0;                                                         // Diameter of measurement wheel in mm
const float MM_PER_REVOLUTION         = PI * WHEEL_DIAMETER;                                          // Linear distance per revolution in mm
const int SAMPLE_SIZE                 = 50;                                                           // Number of samples in moving average window

// Motor Control Constants
const int MIN_TOP_MOTOR_PWM = 0;                                                                      // Minimum PWM duty cycle value for top motor
const int MAX_TOP_MOTOR_PWM = 4095 * (MAX_TOP_MOTOR_POWER / MOTOR_VOLTAGE);                           // Maximum PWM duty cycle value for top motor, calculated at max power for motor
const int MIN_BOTTOM_MOTOR_PWM = 0;                                                                   // Minumum PWM duty cycle value for bottom motor
const int MAX_BOTTOM_MOTOR_PWM = 4095 * (MAX_BOTTOM_MOTOR_POWER / MOTOR_VOLTAGE);                     // Maximum PWM duty cycle value for bottom motor, calculated at max power for motor
int topMotorPWM = 0;     // Current PWM value for top motor
int bottomMotorPWM = 0;  // Current PWM value for bottom motor

// PID Control Variables
float Kp = 400.0;   
float Ki = 0.5;    
float Kd = 1.0;    
float velocityIntegral = 0;
float lastVelocityError = 0;
unsigned long lastVelocityPIDTime = 0;
const float INTEGRAL_MAX = 1000.0;

// Encoder Variables
volatile uint16_t lastPosition = 0;                                                                     // Previous encoder position (0-4095)
volatile float velocities[SAMPLE_SIZE];                                                                 // Circular buffer of velocity measurements
volatile int velocityIndex = 0;                                                                         // Current index in velocity buffer
volatile uint32_t lastSampleTime = 0;                                                                   // Last sample time in microseconds
volatile float targetVelocity = 0;                                                                      // Target velocity for wire

// Wire loading and unloading variables 
bool wireLoadingMode = false;
uint16_t loadingModeLastPosition = 0;
const float LOADING_PWM_SCALE = 500.0;                                                                   // PWM per revolution scaling factor
const int WIRE_LOADING_BOTTOM_TOOL_PWM = MAX_BOTTOM_MOTOR_PWM;

// State Variables
String inputBuffer = "";
bool fatalErrorActive = false;
String errorMessage = "";
bool wireIsLoaded = false;
float targetCurrent = 0;                     // Target motor current for tension control
float actualCurrent = 0;                     // Measured motor current
int safetyCheckCounter = 0;                  // Counter for safety check timing

// Timer Structure
repeating_timer mainTimer;                   // 10ms timer for all periodic tasks

// Telemetry Data Structure
struct Telemetry {
    float targetVelocity;
    float actualVelocity;
    float velocityError;
    float targetCurrent;
    float actualTopCurrent;     
    float actualBottomCurrent;  
    float currentError;
    bool wireStatus;
    bool errorStatus;
    String errorMsg;
    int topPWM;
    int bottomPWM;
} telemetryData;

float readMotorCurrent(int sensorPin, float voltageOffset) {
    // Read raw voltage from current sensor (0-3.3V based on 12-bit ADC)
    float voltage = analogRead(sensorPin) * (3.3 / 4096.0);
    
    // Convert to mA using sensitivity and offset
    return abs(((voltage - voltageOffset) / CURRENT_SENSOR_SENSITIVITY) * 1000.0);
  }

float calculateAverageCurrent(float readings[], int numSamples) {
    float sum = 0;
    for(int i = 0; i < numSamples; i++) {
        sum += readings[i];
    }
    return sum / numSamples;
  }
void updateCurrentReadings() {
    // Read new current values
    topCurrentReadings[currentReadingIndex] = readMotorCurrent(TOP_MOTOR_ACS723, topVoltageOffset);
    bottomCurrentReadings[currentReadingIndex] = readMotorCurrent(BOTTOM_MOTOR_ACS723, bottomVoltageOffset);
    
    // Update circular buffer index
    currentReadingIndex = (currentReadingIndex + 1) % CURRENT_AVERAGE_SAMPLES;
  }
void calibrateCurrentSensors() {
    float topSum = 0;
    float bottomSum = 0;
    
    Serial.println("Calibrating current sensors...");
    
    // Ensure motors are off
    applyTopMotorPWM(0);
    applyBottomMotorPWM(0);
    
    // Small delay to ensure motors are stopped
    delay(1000);
    
    // Take multiple readings and average them
    for(int i = 0; i < CALIBRATION_SAMPLES; i++) {
        topSum += analogRead(TOP_MOTOR_ACS723) * (3.3 / 4096.0);
        bottomSum += analogRead(BOTTOM_MOTOR_ACS723) * (3.3 / 4096.0);
        delay(10);  // Short delay between readings
    }
    
    // Calculate average offsets
    topVoltageOffset = topSum / CALIBRATION_SAMPLES;
    bottomVoltageOffset = bottomSum / CALIBRATION_SAMPLES;
    
    //Serial.print("Top current sensor offset: ");
    //Serial.print(topVoltageOffset, 3);
    //Serial.println("V");
    //Serial.print("Bottom current sensor offset: ");
    //Serial.print(bottomVoltageOffset, 3);
    //Serial.println("V");
  }
void applyTopMotorPWM(int pwmValue) { // Function to apply PWM value to top motor

    // Constrain PWM value within safe limits
    int safePWM;
    
    if (pwmValue > 0) {
        // Forward direction
        safePWM = min(pwmValue, MAX_TOP_MOTOR_PWM);
        safePWM = max(safePWM, MIN_TOP_MOTOR_PWM);
        analogWrite(TOP_MOTOR_DRV8871_IN1, safePWM);
        analogWrite(TOP_MOTOR_DRV8871_IN2, 0);
        topMotorPWM = safePWM;
    } 
    else if (pwmValue < 0) {
        // Reverse direction
        safePWM = min(-pwmValue, MAX_TOP_MOTOR_PWM);
        safePWM = max(safePWM, MIN_TOP_MOTOR_PWM);
        analogWrite(TOP_MOTOR_DRV8871_IN1, 0);
        analogWrite(TOP_MOTOR_DRV8871_IN2, safePWM);
        topMotorPWM = -safePWM;
    }
    else {
        // Stop
        analogWrite(TOP_MOTOR_DRV8871_IN1, 0);
        analogWrite(TOP_MOTOR_DRV8871_IN2, 0);
        topMotorPWM = 0;
    }
  }
void applyBottomMotorPWM(int pwmValue) { // Function to apply PWM value to bottom motor

    // Constrain PWM value within safe limits
    int safePWM;
    
    if (pwmValue > 0) {
        // Forward direction
        safePWM = min(pwmValue, MAX_BOTTOM_MOTOR_PWM);
        safePWM = max(safePWM, MIN_BOTTOM_MOTOR_PWM);
        analogWrite(BOTTOM_MOTOR_DRV8871_IN1, safePWM);
        analogWrite(BOTTOM_MOTOR_DRV8871_IN2, 0);
        bottomMotorPWM = safePWM;
    }
    else if (pwmValue < 0) {
        // Reverse direction
        safePWM = min(-pwmValue, MAX_BOTTOM_MOTOR_PWM);
        safePWM = max(safePWM, MIN_BOTTOM_MOTOR_PWM);
        analogWrite(BOTTOM_MOTOR_DRV8871_IN1, 0);
        analogWrite(BOTTOM_MOTOR_DRV8871_IN2, safePWM);
        bottomMotorPWM = -safePWM;
    }
    else {
        // Stop
        analogWrite(BOTTOM_MOTOR_DRV8871_IN1, 0);
        analogWrite(BOTTOM_MOTOR_DRV8871_IN2, 0);
        bottomMotorPWM = 0;
    }
  }







uint16_t readRawAngle() { // Read raw angle from AS5600 encoder
    Wire.beginTransmission(AS5600_ADDR);
    Wire.write(REG_RAW_ANGLE_H);
    Wire.endTransmission(false);
    Wire.requestFrom(AS5600_ADDR, 2);
    
    if(Wire.available() <= 2) {
        uint16_t high = Wire.read();
        uint16_t low = Wire.read();
        return (high << 8) | low;
    }
    return 0;
  }

float calculateAverageVelocity() { // Calculate average velocity from samples
    float sum = 0;
    for(int i = 0; i < SAMPLE_SIZE; i++) {
        sum += velocities[i];
    }
    return sum / SAMPLE_SIZE;
  }

void triggerFatalError(String message) { // Handle fatal errors
  fatalErrorActive = true;
  errorMessage = message;
    
  // Stop all motors
  analogWrite(TOP_MOTOR_DRV8871_IN1, 0);
  analogWrite(TOP_MOTOR_DRV8871_IN2, 0);
  analogWrite(BOTTOM_MOTOR_DRV8871_IN1, 0);
  analogWrite(BOTTOM_MOTOR_DRV8871_IN2, 0);
    
  digitalWrite(STATUS_LED, LOW);
  Serial.print("FATAL ERROR: ");
  Serial.println(message);
  }

bool checkSafetyLimits() { // Check safety limits
    // Check if values are within allowed ranges
    if(telemetryData.targetVelocity > MAX_VELOCITY || telemetryData.targetVelocity < MIN_VELOCITY) {
        char errorMsg[50];
        snprintf(errorMsg, sizeof(errorMsg), "Target velocity out of range: %.2f mm/s", telemetryData.targetVelocity);
        triggerFatalError(errorMsg);
        return false;
    }
    
    if(telemetryData.targetCurrent > MAX_CURRENT || telemetryData.targetCurrent < MIN_CURRENT) {
        char errorMsg[50];
        snprintf(errorMsg, sizeof(errorMsg), "Target current out of range: %.2f mA", telemetryData.targetCurrent);
        triggerFatalError(errorMsg);
        return false;
    }
    
    // Check for excessive errors
    float velocityError = abs(telemetryData.velocityError);
    if(velocityError > MAX_VELOCITY_ERROR && telemetryData.targetVelocity != 0) {
        char errorMsg[50];
        snprintf(errorMsg, sizeof(errorMsg), "Velocity error too high: %.2f mm/s", velocityError);
        triggerFatalError(errorMsg);
        return false;
    }
    
    float currentError = abs(telemetryData.currentError);
    if(currentError > MAX_CURRENT_ERROR && telemetryData.targetCurrent != 0) {
        char errorMsg[50];
        snprintf(errorMsg, sizeof(errorMsg), "Current error too high: %.2f mA", currentError);
        triggerFatalError(errorMsg);
        return false;
    }
    
    return true;
  }

bool getTelemetryCallback(struct repeating_timer *t) {
   // Velocity telemetry
   telemetryData.targetVelocity = targetVelocity;
   telemetryData.actualVelocity = calculateAverageVelocity();
   telemetryData.velocityError = targetVelocity - telemetryData.actualVelocity;

   // Current telemetry
   telemetryData.targetCurrent = targetCurrent;
   
   // Read raw voltage from current sensors (0-3.3V based on 12-bit ADC)
   float topVoltage = analogRead(TOP_MOTOR_ACS723) * (3.3 / 4096.0);
   float bottomVoltage = analogRead(BOTTOM_MOTOR_ACS723) * (3.3 / 4096.0);


  // Get motor 
  telemetryData.actualTopCurrent = calculateAverageCurrent(topCurrentReadings, CURRENT_AVERAGE_SAMPLES);
  telemetryData.actualBottomCurrent = calculateAverageCurrent(bottomCurrentReadings, CURRENT_AVERAGE_SAMPLES);
  telemetryData.currentError = abs(targetCurrent - telemetryData.actualBottomCurrent);

   // Status telemetry
   telemetryData.wireStatus = wireIsLoaded;
   telemetryData.errorStatus = fatalErrorActive;
   telemetryData.errorMsg = errorMessage;
   
   // Motor PWM telemetry
   telemetryData.topPWM = topMotorPWM;
   telemetryData.bottomPWM = bottomMotorPWM;

  //Serial.print("Raw ADC: "); 
  //Serial.println(analogRead(BOTTOM_MOTOR_ACS723));
  //Serial.print("Voltage: ");
  //Serial.println(bottomVoltage, 4);
  //Serial.print("Offset: ");
  //Serial.println(bottomVoltageOffset, 4);

   return true;
  }

void outputTelemetry() {
    Serial.println("TELEMETRY_BEGIN");
    
    Serial.print("Target Velocity: ");
    Serial.print(telemetryData.targetVelocity, 2);
    Serial.println(" mm/s");
    Serial.print("Actual Velocity: ");
    Serial.print(telemetryData.actualVelocity, 2);
    Serial.println(" mm/s");
    Serial.print("Velocity Error: ");
    Serial.print(telemetryData.velocityError, 2);
    Serial.println(" mm/s");
    
    Serial.print("Target Current: ");
    Serial.print(telemetryData.targetCurrent, 2);
    Serial.println(" mA");
    Serial.print("Top Motor Current: ");       // Add this line
    Serial.print(telemetryData.actualTopCurrent, 2);  // Add this line
    Serial.println(" mA");                     // Add this line
    Serial.print("Bottom Motor Current: ");    // Modified line
    Serial.print(telemetryData.actualBottomCurrent, 2);
    Serial.println(" mA");
    Serial.print("Current Error: ");
    Serial.print(telemetryData.currentError, 2);
    Serial.println(" mA");
    
    Serial.print("Top Motor PWM: ");
    Serial.println(telemetryData.topPWM);
    Serial.print("Bottom Motor PWM: ");
    Serial.println(telemetryData.bottomPWM);
    
    Serial.print("Wire Status: ");
    Serial.println(telemetryData.wireStatus ? "LOADED" : "UNLOADED");
    Serial.print("Error Status: ");
    Serial.println(telemetryData.errorStatus ? telemetryData.errorMsg : "NO ERROR");
    
    Serial.println("TELEMETRY_END");
  }

bool mainTimerCallback(struct repeating_timer *t) { // Combined callback for all periodic tasks
    // Position sampling
    uint32_t currentTime = micros();
    uint16_t currentPosition = readRawAngle();
    
    int16_t deltaPos = currentPosition - lastPosition;
    if(deltaPos < -2048) deltaPos += 4096;  // Handle rollover in positive direction
    if(deltaPos > 2048) deltaPos -= 4096;   // Handle rollover in negative direction

    // Add debug prints
    //Serial.print("Position: ");
    //Serial.print(currentPosition);
    //Serial.print(" Delta: ");
    //Serial.println(deltaPos);
    
    
    if (abs(deltaPos) < 2) {  // Noise threshold
        velocities[velocityIndex] = 0;
        velocityIndex = (velocityIndex + 1) % SAMPLE_SIZE;
        lastPosition = currentPosition;
        lastSampleTime = currentTime;
    } else {
        float timeElapsed = (currentTime - lastSampleTime) / 1000000.0;  // Convert to seconds
        if (timeElapsed >= 0.001) {  // Minimum time threshold
            float rotationFraction = deltaPos / 4096.0;
            float linearDistance = rotationFraction * MM_PER_REVOLUTION;
            velocities[velocityIndex] = linearDistance / timeElapsed;
            velocityIndex = (velocityIndex + 1) % SAMPLE_SIZE;
            lastPosition = currentPosition;
            lastSampleTime = currentTime;
            
            // Add debug print
            //Serial.print("Calculated velocity: ");
            //Serial.println(velocities[velocityIndex]);
        }
    }
    // Update current readings
    updateCurrentReadings();
    // Telemetry collection
    getTelemetryCallback(t);
    // Will run if device is in wire loading mode
    updateLoadingMode();

    // Safety check every ERROR_CHECK_INTERVAL ms
    safetyCheckCounter++;
    if (safetyCheckCounter >= (ERROR_CHECK_INTERVAL / 10)) {
        safetyCheckCounter = 0;
        if (!fatalErrorActive) {
            checkSafetyLimits();
        }
    }

    return true;
  }
void updateLoadingMode() {
    if (!wireLoadingMode) return;
    
    // Get the averaged bottom motor current
    float bottomCurrent = calculateAverageCurrent(bottomCurrentReadings, CURRENT_AVERAGE_SAMPLES);
    
    Serial.println(bottomCurrent);

    if (bottomCurrent > 200.0) {
        wireLoadingMode = false;
        wireIsLoaded = true;  // Wire is now loaded
        applyTopMotorPWM(0);  // Stop top motor
        applyBottomMotorPWM(0); // Stop bottom motor
        Serial.println("Wire detected - exiting loading mode");
        return;
    }
    
    //enable bottom motor to catch wire
    applyBottomMotorPWM(WIRE_LOADING_BOTTOM_TOOL_PWM);
    
    uint16_t currentPosition = readRawAngle();
    int16_t deltaPos = currentPosition - loadingModeLastPosition;
    
    // Handle rollover
    if(deltaPos < -2048) deltaPos += 4096;
    if(deltaPos > 2048) deltaPos -= 4096;
    
    // Calculate motor PWM based on encoder movement
    if (abs(deltaPos) > 2) {  // Noise threshold
        int pwmValue = (int)(deltaPos * LOADING_PWM_SCALE);
        applyTopMotorPWM(pwmValue);
        loadingModeLastPosition = currentPosition;
    } else {
        applyTopMotorPWM(0);  // Stop if no significant movement
    }
  }
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
void loop() {
   // Process serial commands
   while (Serial.available()) {
       char inChar = (char)Serial.read();
       if (inChar != '\n') {
           inputBuffer += inChar;
       }
       else {
           inputBuffer.trim();
           if (inputBuffer.length() > 0) {
               processCommand(inputBuffer);
           }
           inputBuffer = "";
       }
   }

   // Handle error recovery if reset command received
   if (fatalErrorActive) {
       digitalWrite(STATUS_LED, !digitalRead(STATUS_LED));  // Blink LED
       delay(100);
   }
}

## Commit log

2024-06-03 added CAD, firmware, & images
    [printer.cfg]
2024-06-03 added images of motor banks and e-box
2024-06-26 added requirements doc
    [printer.cfg]
2024-08-02 updated wire EDM toolhead sections
2024-08-19 updated requirements with wire tension specs
    [betta-wire-engineering-calculations.xlsx]
2024-08-21 IP68 limit switch
    [IP68-limit-switch.kicad_pcb, IP68-limit-switch.kicad_sch, IP68-limit-switch_RevA.step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]
2024-08-21 updated constraints to 0.2 mm diameter wire
    [betta-wire-engineering-calculations.xlsx]
2024-10-21 Hardware Section Update
    Updated fastener material. Extra information on fastener selection. Stressed pin selection. Made size requirements more clear while leaving them open. Typo fix.
    Added segment to aquarium sizing. Called out required minimum tank size. Called out common tank sizes likely to work well.
2024-10-23 Clarified features. Added QoL section.
    Mentioned kinematic fixes and stainless steel use.
    Added QoL section. Outlined several important changes that improve user QoL.
2024-10-23 Addition to QoL Segment
    Added cable chain requirement.
2025-01-17 RevB of Limit Switch
    - switched from TH JST-XH to SMD JST-PH
    - Minimized size down to volume of connector
    - added LCSC part numbers for JLCPCB assembly
    [IP68-limit-switch.kicad_pcb, IP68-limit-switch_RevA.step, S3B-PH-SM4-TB.step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]
2025-01-17 toolhead-rod-energized
    - SMD connectors with ring terminals
    - 6A 300VMAX
    [bom.csv, designators.csv, positions.csv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]
2025-01-19 file reorganization
    [bom.csv, designators.csv, positions.csv]
2025-01-31 firmware for wire tool added
    - implemented wire velocity reporting over serial for prototype testing with AS5600 encoder
    - renamed electronics folder to circuit-boards
    [S3B-PH-SM4-TB.step, bom.csv, designators.csv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]
2025-01-31 Update wire-tool-firmware.ino
    - commands for all functions run properly
    - telemetry reporting added
    - emergency reset behavior added
    [wire-tool-firmware.ino]
2025-01-31 ready for PID loop implementation
2025-02-01 PID loop added for velocity
    PID loop functional, but not tuned
2025-02-01 Update wire-tool-firmware.ino
    implemented current sensing and motor driving for both top and bottom tools
2025-02-01 Update wire-tool-firmware.ino
    - implemented semi-automaic loading of wire
    - debugged current sensors
2025-02-12 added rack controller motherboard RevA
    [430450409.step, ESQ-120-23-T-D.step, S3B-PH-SM4-TB.step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]
2025-02-13 schematic for control board revised
    [2601-1102.stp, LMR36520ADDAR.stp, S3B-XH-SM4-TB.STEP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]
2025-02-13 updated 48V->5V buck to 3A
    [0679H9120-05.step, LV14360PDDAR.stp, power.kicad_sch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]
2025-02-18 Completed control board revB`
    - fixed UART bus
    - fixed pullup and pulldown resistors
    -layout completed for new board outline
    [0679H9120-05.step, 2601-1102.stp, 430450409.step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]
2025-03-07 modified BoM & STEPs for export
    [rack-controller-V1.0.kicad_pcb]
2025-03-12 Removed Spring Conn Rod Energizer
    [bom.csv, designators.csv, positions.csv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]
2025-03-13 removed UART
    [motor_drivers.kicad_sch, power.kicad_sch, rack-controller-V1.0.kicad_pcb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]
2025-03-13 rack controller revC production files
    - Removed UART
    - Added resistors for microstep selection
    - Renamed connectors starting from index 0
    - Fixed Pi PSU GND error from RevB
    - Reduced layers from 6 to 4
    [bom.csv, designators.csv, motor_drivers.kicad_sch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]
2025-03-13 magnetic endstop revC
    - Changed connector to JST-XH, SMD version
    - 16 mm x 20 mm
    - Do-not-populate LED
    [S3B-PH-SM4-TB.step, S3B-XH-SM4-TB.STEP, bom.csv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]
2025-04-25 schematic for BDC motor drivers 00 and 01
    [BDC_motor_drivers.kicad_sch, DRV8235RTER.stp, motor_drivers.kicad_sch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]
2025-04-26 layout of revD
    [bom.csv, designators.csv, positions.csv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]
2025-05-05 Update README.md with new features
    Added assisted threading and hole popping as confirmed features along with short descriptions.
2025-05-31 N30 Motor Board
    [N30-motor-board-RevA.step, N30-motor-board.kicad_pcb, N30-motor-board.kicad_sch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]
2025-07-27 updated text in schematic
    [magnetic-limit-switch.kicad_sch]
2025-07-27 increased number of stitching vias for ground planes
    [magnetic-limit-switch.kicad_pcb, magnetic-limit-switch.kicad_sch]
2025-07-29 RevE of Rack Controller
    - Improved BDC drivers for I2C control
    - Removed aluminum polymer caps
    - Added fan vent hole
    - Rerouted
    - Added ferrites on BDC output
    [BDC_motor_drivers.kicad_sch, bom.csv, designators.csv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]
2025-08-20 magnetic endstop revD
    - improved silkscreen
    - DNP connector (solder to pads)
    - strain relief for wires
    [bom.csv, designators.csv, magnetic-limit-switch-D.step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]
2025-11-17 Rack-Controller-Rev-F
    - 3 channel high-side power switches
    - 5 stepper motor driver sockets
    - 2 brushed dc motor drivers with selection between 24V and 9V
    [9V_brushless_motor_drivers.kicad_sch, BDC_motor_drivers.kicad_sch, bom.csv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]

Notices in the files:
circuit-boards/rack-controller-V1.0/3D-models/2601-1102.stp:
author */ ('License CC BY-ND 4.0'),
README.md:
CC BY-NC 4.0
